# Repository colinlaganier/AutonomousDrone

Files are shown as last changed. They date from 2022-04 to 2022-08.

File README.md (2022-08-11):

# Autonomous Indoor Drone Sanitation System

## Description  

Created by Colin Laganier under the supervision of Prof. Robert Shorten as part of the MEng Final Year Project. 

Progress can be followed on the regularly update logbook for additional information about the project: [https://bit.ly/3Ni6ypL](https://bit.ly/3Ni6ypL)

## Hardware

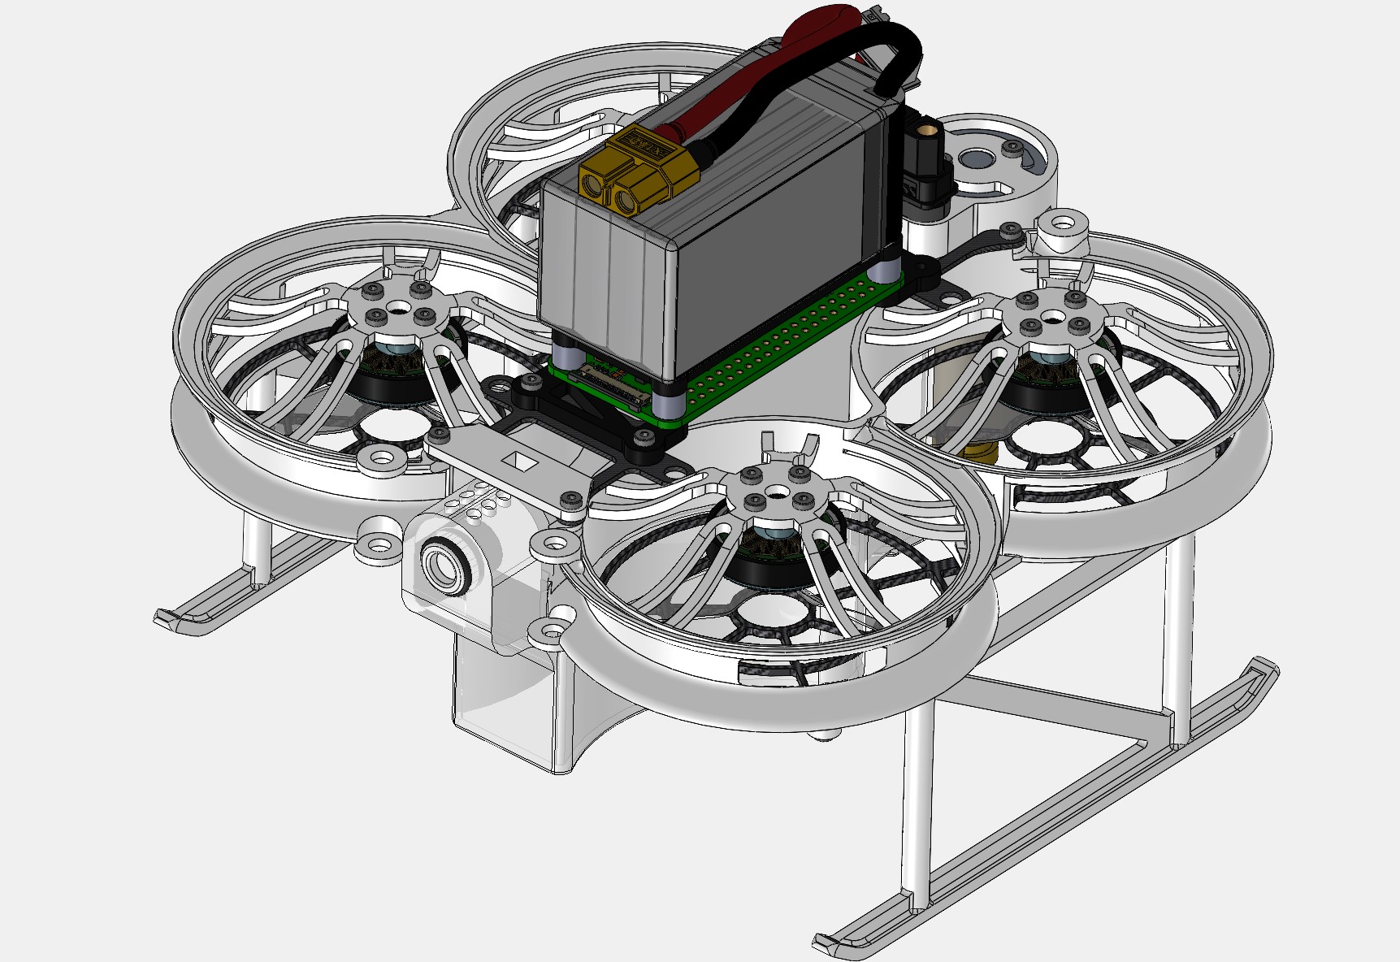
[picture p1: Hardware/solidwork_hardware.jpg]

<sub>Solidworks Hardware Assembly</sub>
<!-- &nbsp; -->
 
The drone is built upon the Diatone Taycan C25 MK2 frame, with 2004 BetaFPV brushless DC Motors and a Flywoo Goku GN745 Flight Controller ESC unit running ArduCopter 4.1.5 firmware. To fit its purpose of a sanitation drone the following pieces were designed and added:
* Transparent Nylon 100mL Water tank, fitted with a refill valve and a silicone coating to ensure watertightness.
* Waterpump and PLA support for spraying of the cleaning solution.
* Acrylic Raspberry Pi Zero support.
* PLA ski-style landing gear support legs.  

The control software is running on a Raspberry Pi Zero 2 W running Debian on each drone, connected to a central PC running Ubuntu 16.04 using a TCP/IP communication.  

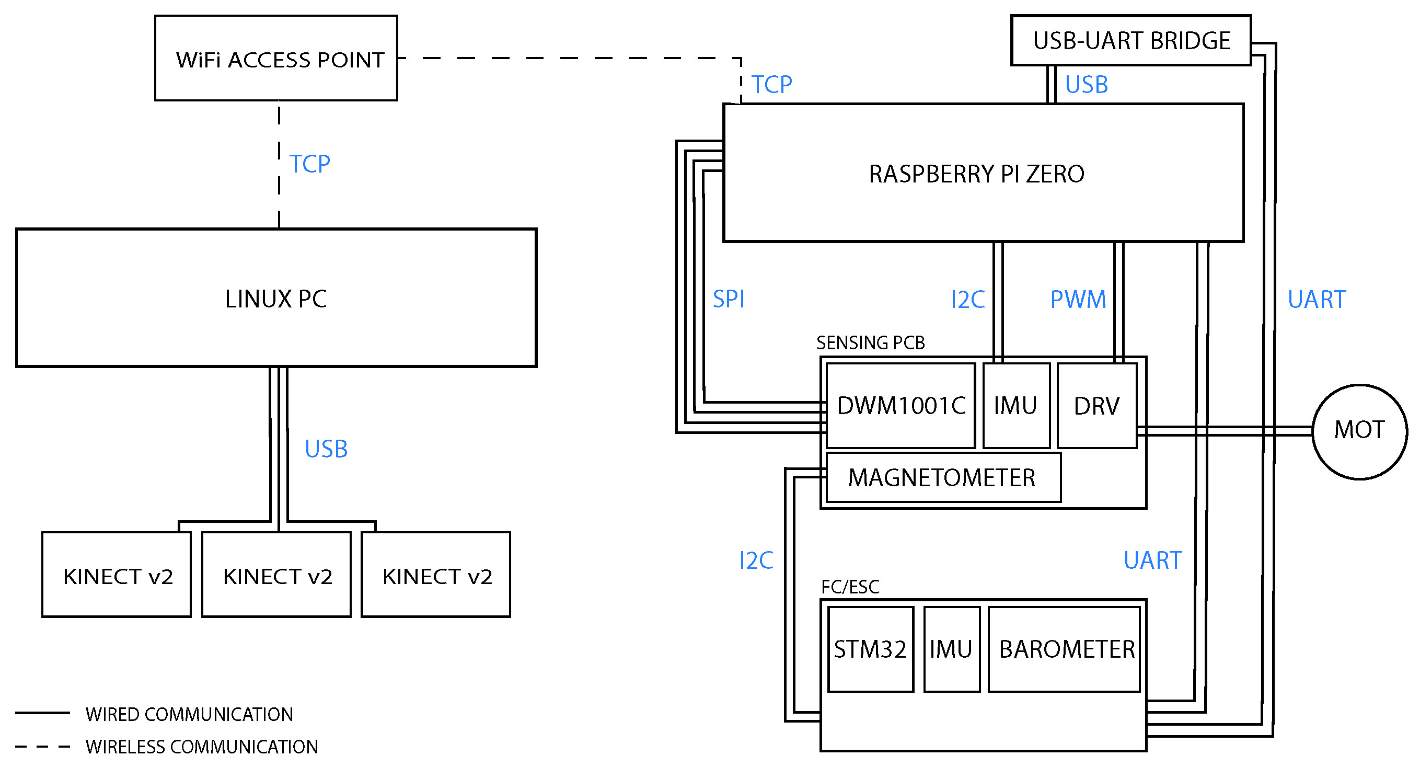
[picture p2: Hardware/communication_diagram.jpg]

<sub>Communication Architecture of Proposed Solution</sub>

## PCB


<sub>Altium Designer PCB Assembly</sub>

A custom PCB was designed to hold together the DWM1001C module from Decawave, as well as a MPU6050 IMU and a QMC5883L Compass for positioning; as well as a DRV8871 to control the spraying pump. The focus of the PCB is ensuring a small footprint to house all of the components on a small size platform. The PCB was designed with Altium Designer and manufactured and assembled by JLCPCB.

## Room Mapping

The room mapping is done using ROS running on an Linux PC using three Kinects v2 and the libfreenect2 driver with CUDA acceleration. The room mapping is done using RTAB-Map to create a 2D grid array of the furniture in the lecture hall. 

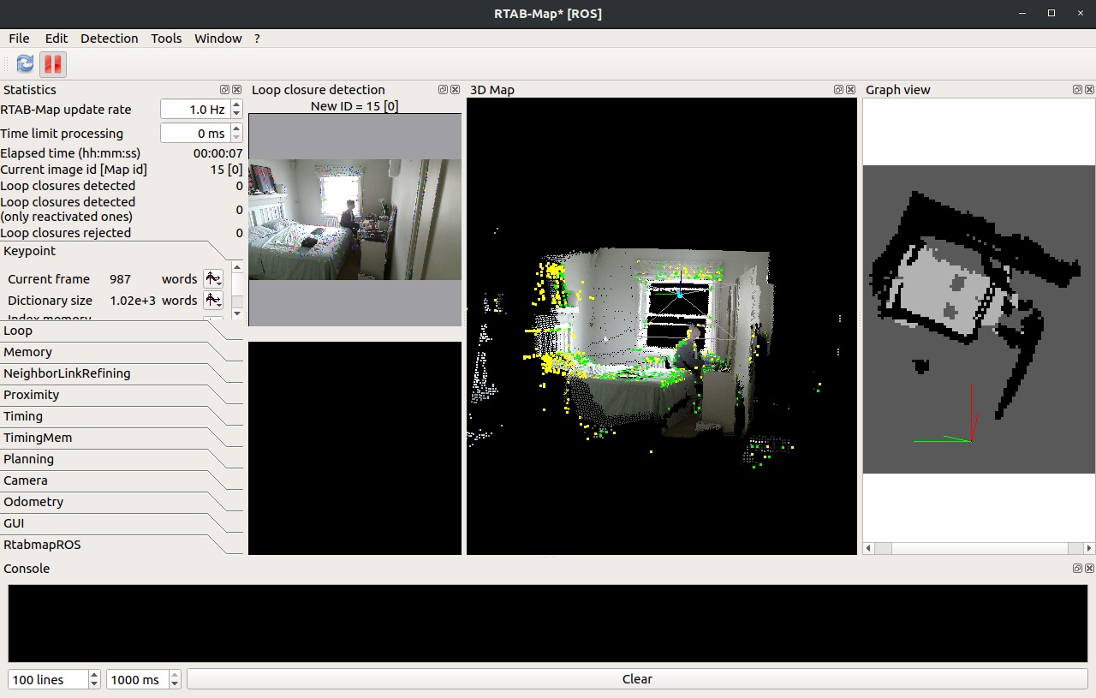
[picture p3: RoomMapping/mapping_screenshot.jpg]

<sub>Screenshot of the RTAB-Map Development GUI</sub>

## Positioning

The positioning system rely on the DWM1001C Ultra-Wideband chip by Decawave and used an asymetric two-way ranging positioning system designed by Decawave. This system provides a sub-20cm positioning error within the tested environment. The ranging data is fetched from the IC by the Raspberry Pi, reformated and fed into the Arducopter Extended Kalman Filtering positioning system where it is combined with IMU, barometer and compass data.

<p align="middle">
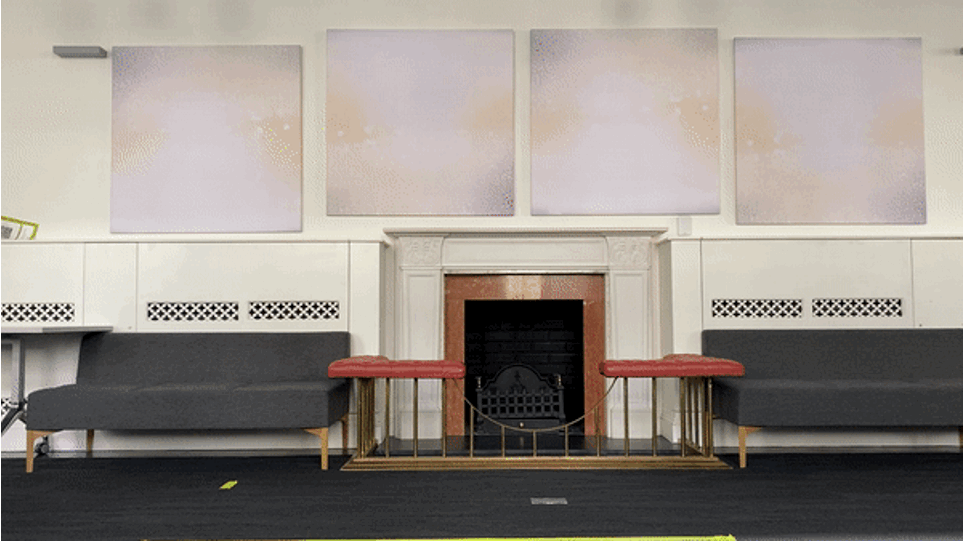
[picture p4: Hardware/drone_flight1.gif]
  
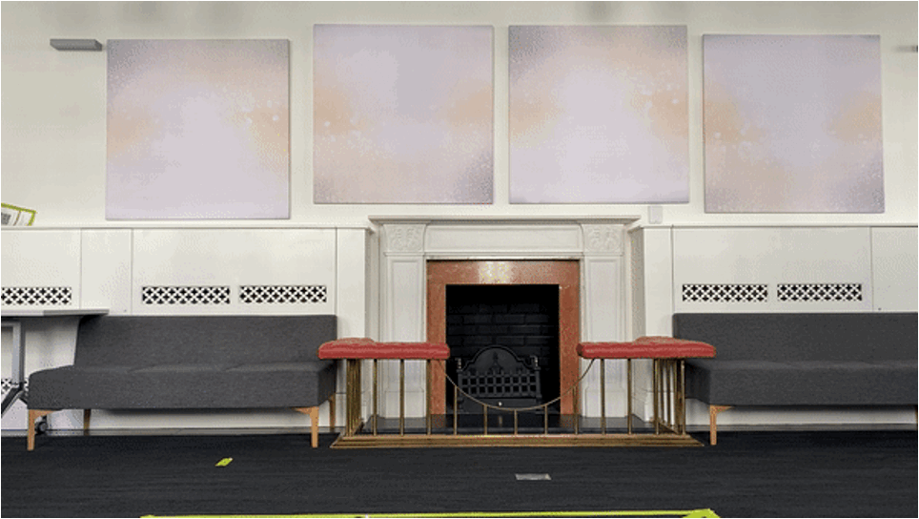
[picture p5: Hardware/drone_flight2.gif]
   
</p>

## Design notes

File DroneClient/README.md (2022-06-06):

# Drone Client

## Description 

This is the source code of the online control loop, positioning and communication. This code should be run on the drone mounted Raspberry Pi. 

To use on the Raspberry Pi, ensure the following packages are installed:
* Mavlink_v2
* WiringPi
* Pthread

To run the code, ensure the server is up and running and enter the following command in the command line from the DroneClient directory: 

```
mkdir build && cd build
cmake ../CMakeLists.txt
make 
./DroneClient
```

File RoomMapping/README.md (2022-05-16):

# Room Mapping

This directory is the ROS process to create the 2D occupancy grid from the Microsoft Kinect v2 RGBD camera using octomap.

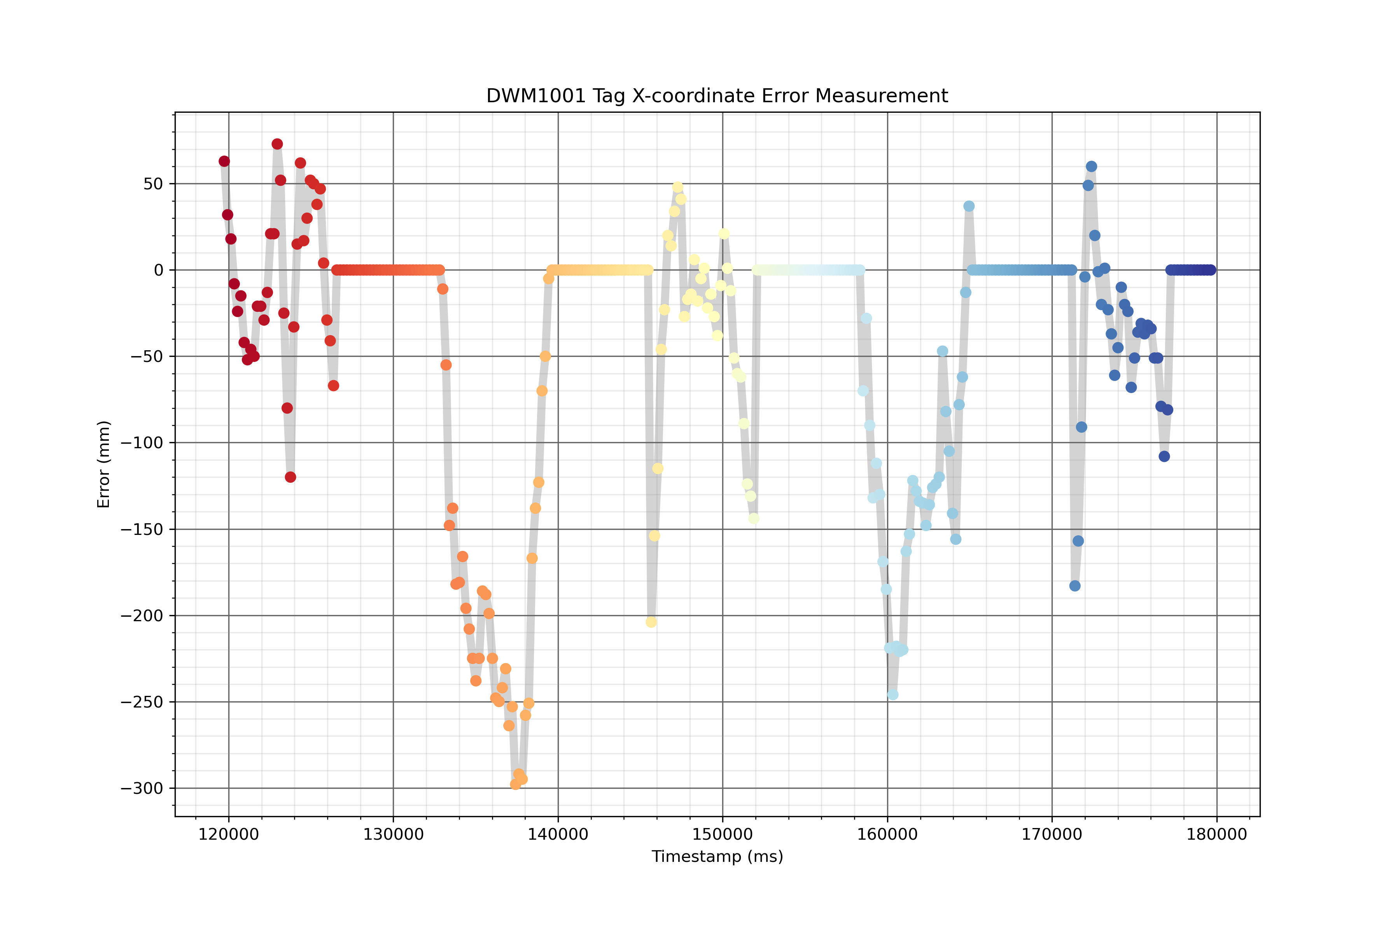
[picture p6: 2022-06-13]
Positioning/Images/error_57_x.png

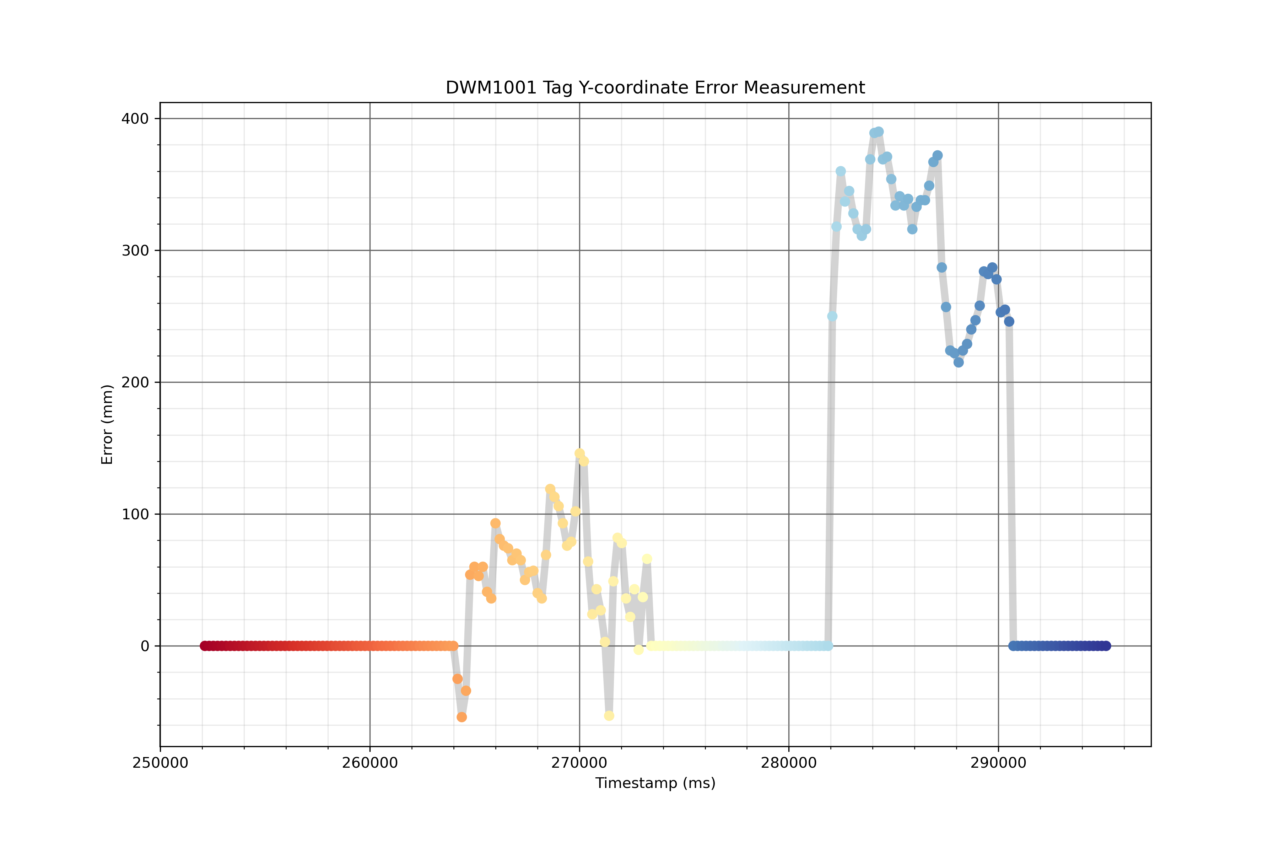
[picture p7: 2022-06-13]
Positioning/Images/error_09_y.png

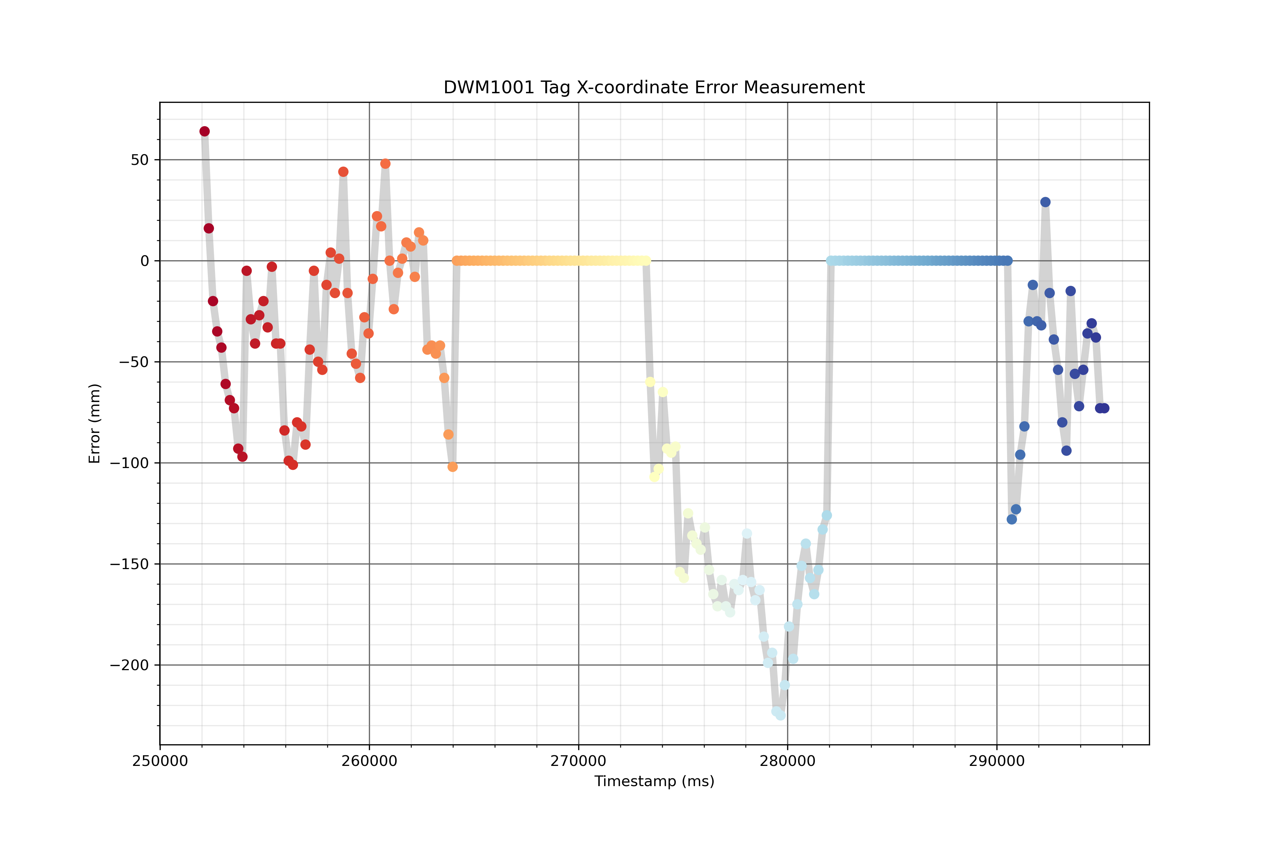
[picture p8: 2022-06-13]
Positioning/Images/error_09_x.png

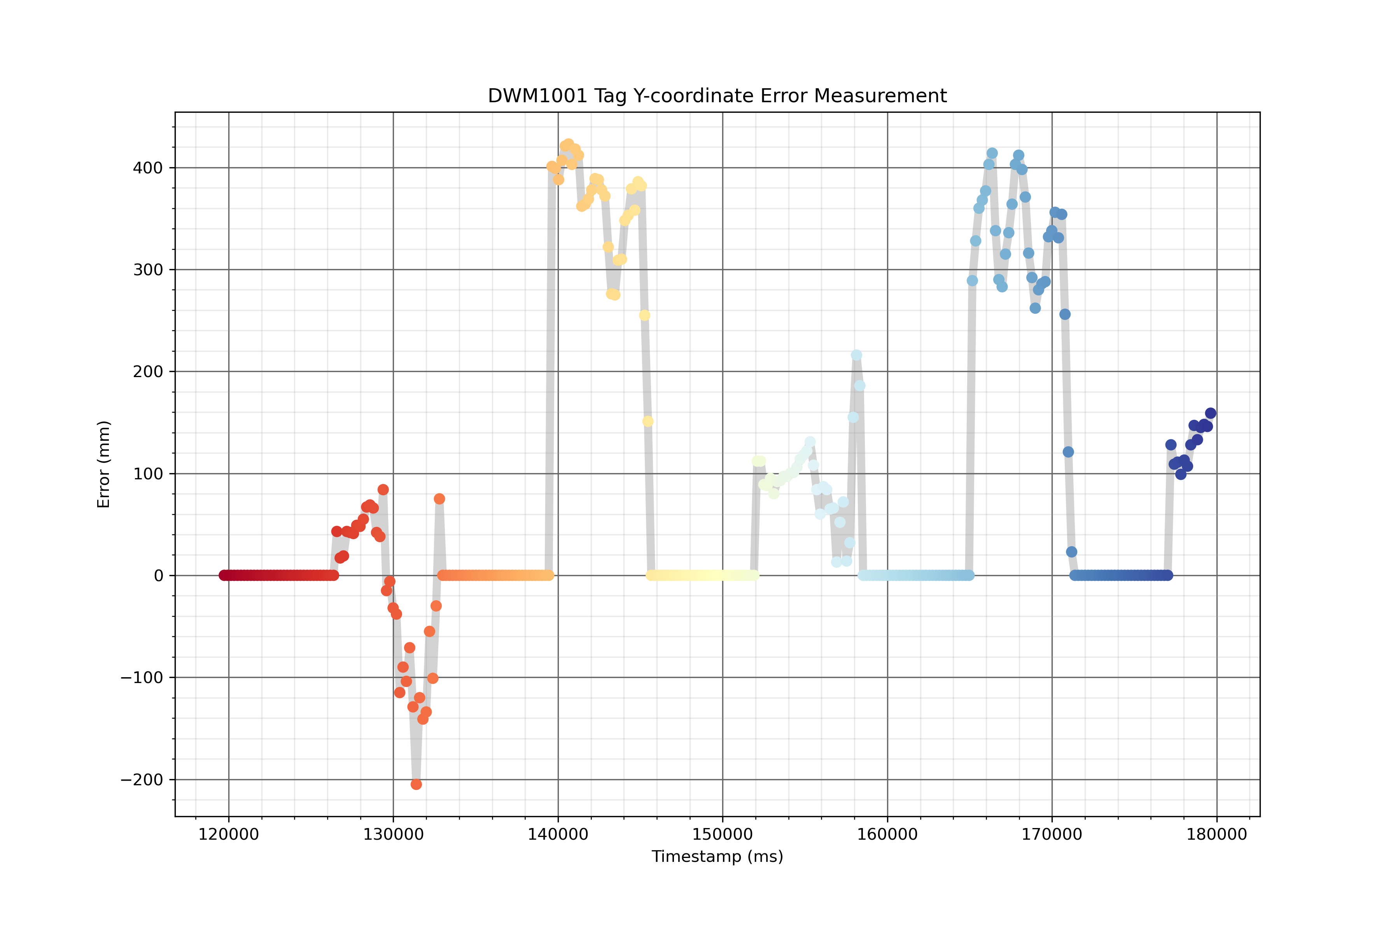
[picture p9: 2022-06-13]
Positioning/Images/error_57_y.png

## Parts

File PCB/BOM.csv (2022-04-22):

Comment | Designator | Footprint | JLCPCB Part # | Description
CL05B104KO5NNNC | C1, C3, C5, C9, C11 | 0402 | C1525 | 16V 100nF X7R ±10% 0402 Multilayer Ceramic Capacitors MLCC - SMD/SMT ROHS
CL05A106MQ5NUNC | C10 | 0402 | C15525 | 6.3V 10uF X5R ±20% 0402 Multilayer Ceramic Capacitors MLCC - SMD/SMT ROHS
EEHZA1J220XV | C2 | CAP-SMD | C454361 | 63V 22uF ±20% 8mm 80mΩ@100kHz 6.3mm 1.5A@100kHz -55℃~+105℃ 10000hrs@105℃ SMD,6.3x8mm Solid Polymer Electrolytic Capacitor ROHS
CL05B103KB5NNNC | C4 | 0402 | C15195 | 50V 10nF X7R ±10% 0402 Multilayer Ceramic Capacitors MLCC - SMD/SMT ROHS
0402B222K500NT | C6 | 0402 | C1531 | 50V 2.2nF X7R ±10% 0402 Multilayer Ceramic Capacitors MLCC - SMD/SMT ROHS
CL05B224KO5NNNC | C8, C12 | 0402 | C16772 | 16V 220nF X7R ±10% 0402 Multilayer Ceramic Capacitors MLCC - SMD/SMT ROHS
KT-0603W | D1, D2, D3 | LED_0603 | C2290 | White 0603 Light Emitting Diodes (LED) RoHS
DRV8871DDAR | IC001 | SOIC-8_3.9x4.9x1.27P | C75864 | SO-8 Motor Driver ICs ROHS
MPU-6050 | IC002 | QFN-24_EP_4.0x4.0x0.5P | C24112 | QFN-24_4x4x05P Attitude Sensors ROHS
QMC5883L | IC003 | LGA-16(3x3x0.9mm) | C976032 | LGA-16(3x3x0.9mm) Magnetic Sensors ROHS
0402WGF3002TCE | R1 | 0402 | C25776 | ±1% 1/16W Thick Film Resistors 50V ±100ppm/℃ -55℃~+155℃ 30kΩ 0402 Chip Resistor - Surface Mount ROHS
0402WGF1002TCE | R2 | 0402 | C25744 | ±1% 1/16W Thick Film Resistors 50V ±200ppm/℃ -55℃~+155℃ 30.1Ω 0402 Chip Resistor - Surface Mount ROHS
0402WGF4701TCE | R3, R4 | 0402 | C25900 | ±1% 1/16W Thick Film Resistors 50V ±100ppm/℃ -55℃~+155℃ 4.7kΩ 0402 Chip Resistor - Surface Mount ROHS
0402WGF0000TCE | R5 | 0402 | C17168 | ±1% 1/16W Thick Film Resistors 50V ±800ppm/℃ -55℃~+155℃ 0Ω 0402 Chip Resistor - Surface Mount ROHS
0402WGF2201TCE | R6, R7 | 0402 | C25879 | ±1% 1/16W Thick Film Resistors 50V ±100ppm/℃ -55℃~+155℃ 2.2kΩ 0402 Chip Resistor - Surface Mount ROHS
0402WGF301JTCE | R8, R9, R10 | 0402 | C67234 | ±1% 1/16W Thick Film Resistors 50V ±200ppm/℃ -55℃~+155℃ 30.1Ω 0402 Chip Resistor - Surface Mount ROHS
B3U-1000P | SW1, SW2 | SW-SMD-2_2.5x3.0x1.6 | C231329 | 2.5mm 1.6mm Round Button 50mA Brick nogging 3mm SPST 12V SMD,2.5x3x1.6mm Tactile Switches ROHS

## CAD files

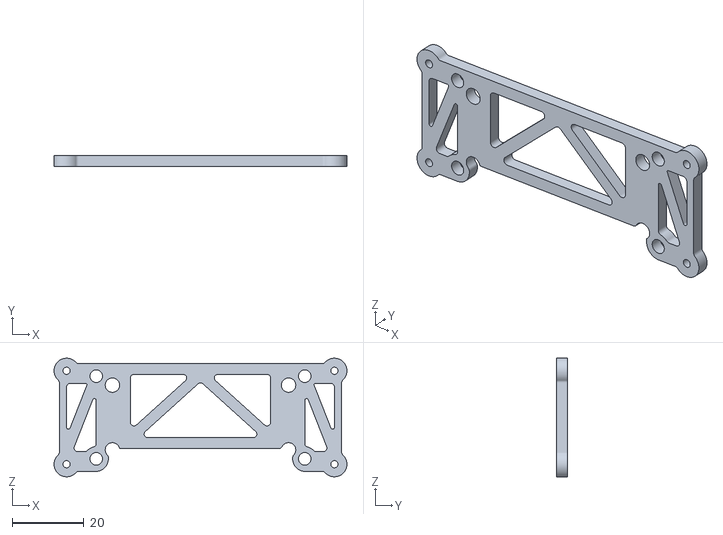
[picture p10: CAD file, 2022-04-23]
Hardware/rasPiSupport_v3.STL
81.5 x 3.00 x 33.0

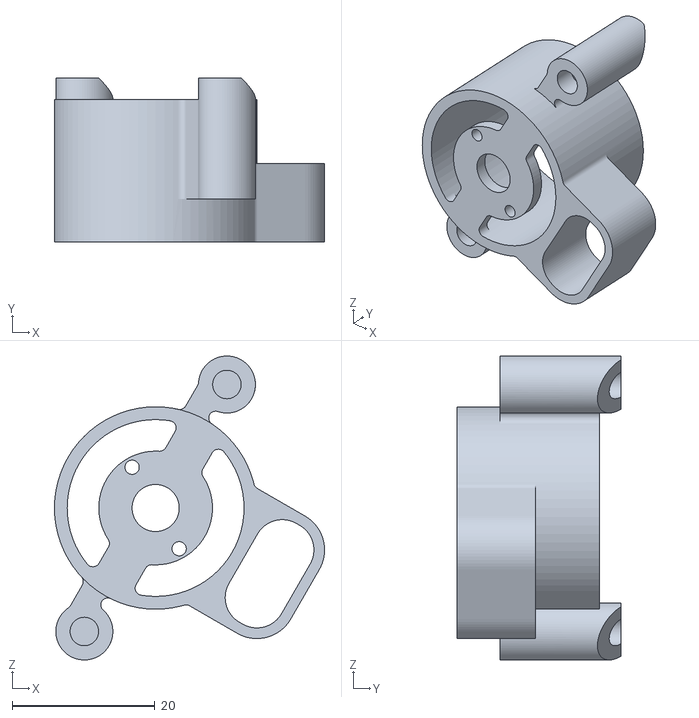
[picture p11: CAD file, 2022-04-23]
Hardware/pumpHolder_v3.STL
37.9 x 23.0 x 42.6

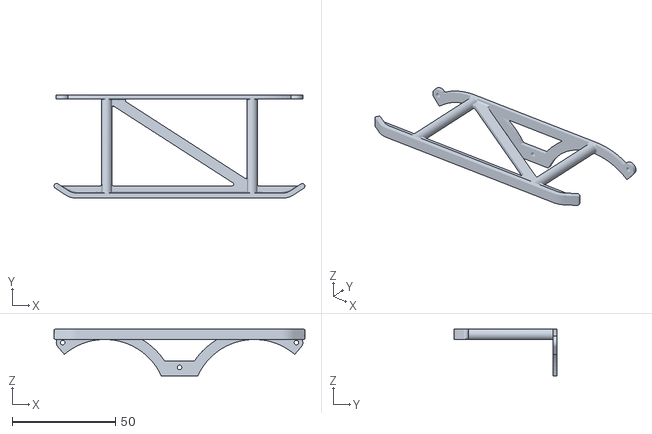
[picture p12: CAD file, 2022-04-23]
Hardware/supportRight_v2.STL
121.3 x 50.0 x 22.6

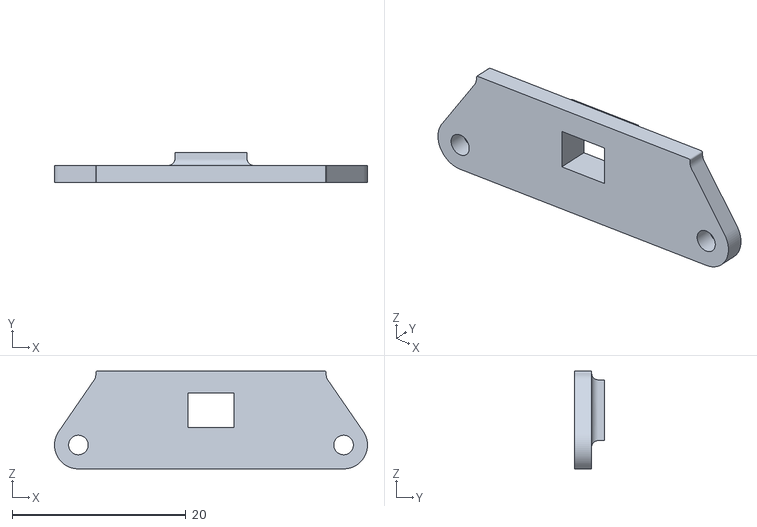
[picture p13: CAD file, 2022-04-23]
Hardware/antennaSupport_v1.STL
36.0 x 3.50 x 11.2

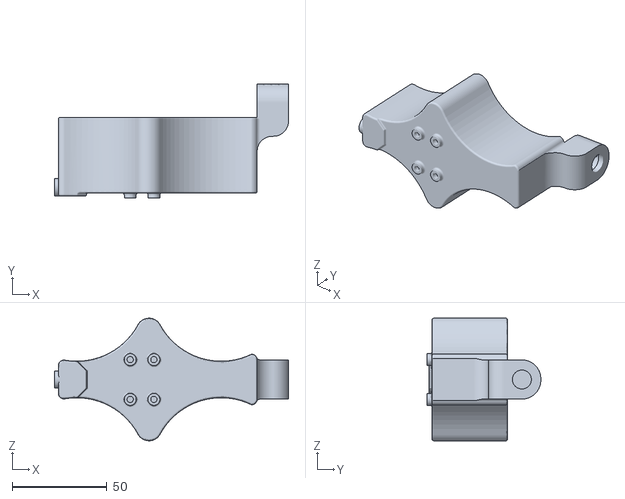
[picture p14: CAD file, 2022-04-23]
Hardware/tank_v7.STL
123.5 x 60.0 x 64.7

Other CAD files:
Hardware/supportLeft_v2.STL

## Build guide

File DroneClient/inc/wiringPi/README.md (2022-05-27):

WiringPi (Unofficial Mirror/Fork)
=================================

This is an unofficial mirror/fork of wiringPi to support ports (Python/Ruby/etc).  With the
[end of official development](http://wiringpi.com/wiringpi-deprecated/), this repository
has become a mirror of the last "official" source release, plus a fork facilitating updates
to support newer hardware (primarily for use by the ports) and fix bugs.

  * The final "official" source release can be found at the
    [`final_source_2.50`](https://github.com/WiringPi/WiringPi/tree/final_official_2.50) tag.
  * The default `master` branch contains code that has been written since that final source
    release to provide support for newer hardware.

Ports
-----

wiringPi has been wrapped for multiple languages:

* Node - https://github.com/WiringPi/WiringPi-Node
* Perl - https://github.com/WiringPi/WiringPi-Perl
* PHP - https://github.com/WiringPi/WiringPi-PHP
* Python - https://github.com/WiringPi/WiringPi-Python
* Ruby - https://github.com/WiringPi/WiringPi-Ruby

Support
-------

Please do not email Gordon if you have issues, he will not be able to help.

Pull-requests may be accepted to add or fix support for newer hardware, but new features or
other changes may not be accepted.

For support, comments, questions, etc please join the WiringPi Discord channel: https://discord.gg/SM4WUVG

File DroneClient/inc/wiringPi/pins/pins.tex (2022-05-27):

\documentclass[12pt,a4paper]{article}
\parskip 1ex
\parindent 0em
\thispagestyle{empty}
\pagestyle{plain}
\pagenumbering{arabic}
\setlength{\topmargin}{0pt}
\setlength{\headheight}{0pt}
\setlength{\headsep}{0pt}
\setlength{\topskip}{0pt}
\setlength{\textheight}{240mm}
\setlength{\footskip}{5ex}
\setlength{\oddsidemargin}{0pt}
\setlength{\evensidemargin}{0pt}
\setlength{\textwidth}{160mm}
\usepackage[dvips]{graphics,color}
\usepackage{helvet}
\renewcommand{\familydefault}{\sfdefault}
\begin{document}
\begin{sffamily}
\definecolor{rtb-black}{rgb}  {0.0, 0.0, 0.0}
\definecolor{rtb-navy}{rgb}   {0.0, 0.0, 0.5}
\definecolor{rtb-green}{rgb}  {0.0, 0.5, 0.0}
\definecolor{rtb-teal}{rgb}   {0.0, 0.5, 0.5}
\definecolor{rtb-maroon}{rgb} {0.5, 0.0, 0.0}
\definecolor{rtb-purple}{rgb} {0.5, 0.0, 0.5}
\definecolor{rtb-olive}{rgb}  {0.5, 0.5, 0.0}
\definecolor{rtb-silver}{rgb} {0.7, 0.7, 0.7}
\definecolor{rtb-grey}{rgb}   {0.5, 0.5, 0.5}
\definecolor{rtb-blue}{rgb}   {0.0, 0.0, 1.0}
\definecolor{rtb-lime}{rgb}   {0.0, 1.0, 0.0}
\definecolor{rtb-aqua}{rgb}   {0.0, 1.0, 1.0}
\definecolor{rtb-red}{rgb}    {1.0, 0.0, 0.0}
\definecolor{rtb-fuchsia}{rgb}{1.0, 0.0, 1.0}
\definecolor{rtb-yellow}{rgb} {1.0, 1.0, 0.0}
\definecolor{rtb-white}{rgb}  {1.0, 1.0, 1.0}

\begin{center}
\bfseries{WiringPi: GPIO Pin Numbering Tables}\\
\tt{https://github.com/WiringPi/WiringPi}
\end{center}

\begin{center}
\begin{tabular}{|c|c|c||p{8mm}|p{8mm}||c|c|c|c|}
\hline
\multicolumn{8}{|c|}{\bfseries{P1: The Main GPIO connector}}\\
\hline
\hline
WiringPi Pin	& BCM GPIO	& Name	& \multicolumn{2}{|c||}{Header}	& Name	& BCM GPIO	& WiringPi Pin\\
\hline
\hline
	& 			& \textcolor{rtb-red}{3.3v}	& \raggedleft{1} &  2 & \textcolor{rtb-maroon}{5v}	& 	& \\
\hline
8	& Rv1:0 - Rv2:2		& \textcolor{rtb-aqua}{SDA}	& \raggedleft{3} &  4 & \textcolor{rtb-maroon}{5v}	& 	& \\
\hline
9	& Rv1:1 - Rv2:3		& \textcolor{rtb-aqua}{SCL}	& \raggedleft{5} &  6 & \textcolor{rtb-black}{0v}	& 	& \\
\hline
7	& 4			& \textcolor{rtb-green}{GPIO7}	& \raggedleft{7} &  8 & \textcolor{rtb-yellow}{TxD}	& 14    & 15\\
\hline
	& 			& \textcolor{rtb-black}{0v}	& \raggedleft{9} & 10 & \textcolor{rtb-yellow}{RxD}	& 15	& 16\\
\hline
0	& 17			& \textcolor{rtb-green}{GPIO0}	& \raggedleft{11} & 12 & \textcolor{rtb-green}{GPIO1}	& 18	& 1\\
\hline
2	& Rv1:21 - Rv2:27	& \textcolor{rtb-green}{GPIO2}	& \raggedleft{13} & 14 & \textcolor{rtb-black}{0v}	& 	& \\
\hline
3	& 22			& \textcolor{rtb-green}{GPIO3}	& \raggedleft{15} & 16 & \textcolor{rtb-green}{GPIO4}	& 23	& 4\\
\hline
	& 			& \textcolor{rtb-red}{3.3v}	& \raggedleft{17} & 18 & \textcolor{rtb-green}{GPIO5}	& 24	& 5\\
\hline
12	& 10			& \textcolor{rtb-teal}{MOSI}	& \raggedleft{19} & 20 & \textcolor{rtb-black}{0v}	& 	& \\
\hline
13	& 9			& \textcolor{rtb-teal}{MISO}	& \raggedleft{21} & 22 & \textcolor{rtb-green}{GPIO6}	& 25	& 6\\
\hline
14	& 11			& \textcolor{rtb-teal}{SCLK}	& \raggedleft{23} & 24 & \textcolor{rtb-teal}{CE0}	& 8	& 10\\
\hline
	& 			& \textcolor{rtb-black}{0v}	& \raggedleft{25} & 26 & \textcolor{rtb-teal}{CE1}	& 7	& 11\\
\hline
\hline
WiringPi Pin	& BCM GPIO	& Name	& \multicolumn{2}{|c||}{Header}	& Name	& BCM GPIO	& WiringPi Pin\\
\hline
\end{tabular}
\end{center}

Note the differences between Revision 1 and Revision 2 Raspberry
Pi's. The Revision 2 is readily identifiable by the presence of the 2
mounting holes.

The revision 2 Raspberry Pi has an additional GPIO connector, P5, which is next to the main P1 GPIO
connector:

\begin{center}
\begin{tabular}{|c|c|c||p{8mm}|p{8mm}||c|c|c|c|}
\hline
\multicolumn{8}{|c|}{\bfseries{P5: Secondary GPIO connector (Rev. 2 Pi only)}}\\
\hline
\hline
WiringPi Pin	& BCM GPIO	& Name	& \multicolumn{2}{|c||}{Header}	& Name	& BCM GPIO	& WiringPi Pin\\
\hline
\hline
	& 		& \textcolor{rtb-maroon}{5v}	& \raggedleft{1} &  2 & \textcolor{rtb-red}{3.3v}	& 	&	\\
\hline
17	& 28		& \textcolor{rtb-green}{GPIO8}	& \raggedleft{3} &  4 & \textcolor{rtb-green}{GPIO9}	& 29	& 18	\\
\hline
19	& 30		& \textcolor{rtb-green}{GPIO10}	& \raggedleft{5} &  6 & \textcolor{rtb-green}{GPIO11}	& 31	& 20	\\
\hline
	& 		& \textcolor{rtb-black}{0v}	& \raggedleft{7} &  8 & \textcolor{rtb-black}{0v}	& 	&	\\
\hline
\hline
WiringPi Pin	& BCM GPIO	& Name	& \multicolumn{2}{|c||}{Header}	& Name	& BCM GPIO	& WiringPi Pin\\
\hline
\end{tabular}
\end{center}

\end{sffamily}
\end{document}

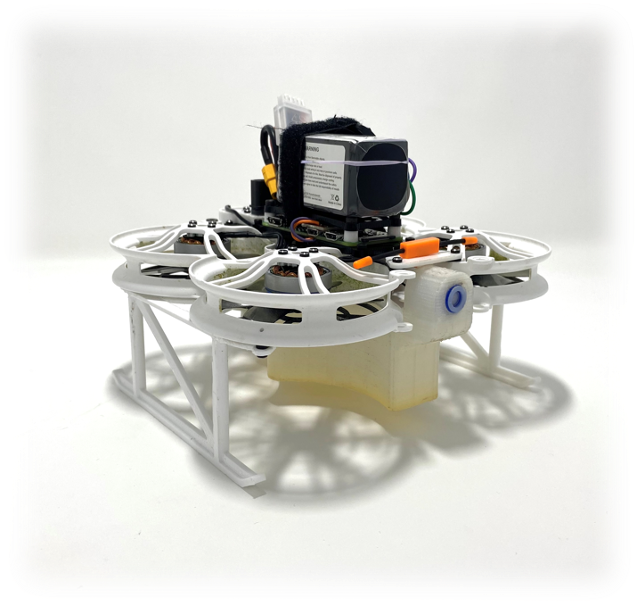
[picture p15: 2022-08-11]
Hardware/drone_assembled.png

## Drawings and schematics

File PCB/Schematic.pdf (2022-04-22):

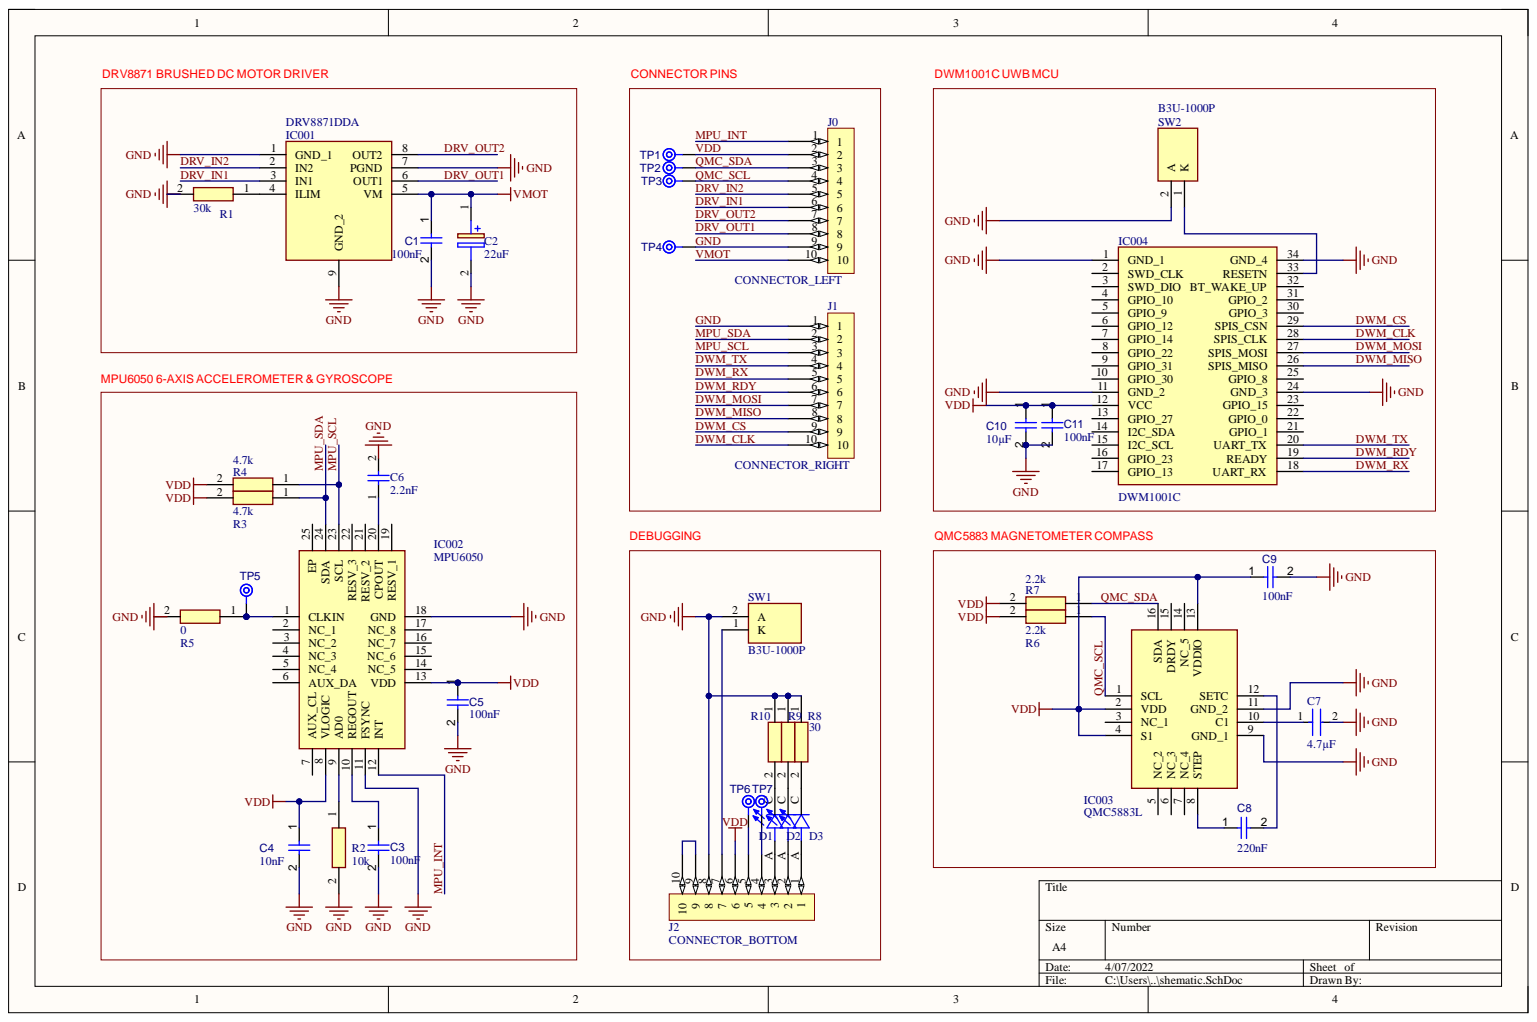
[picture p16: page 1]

1 19 CPOUT 20 RESV_2 21 RESV_3 22 SCL 23 SDA 24 EP 25

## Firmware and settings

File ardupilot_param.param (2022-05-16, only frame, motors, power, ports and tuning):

ATC_ANG_LIM_TC,1
ATC_ANG_PIT_P,18
ATC_ANG_RLL_P,18
ATC_ANG_YAW_P,10
ATC_ANGLE_BOOST,1
ATC_RAT_PIT_D,0.002
ATC_RAT_PIT_FF,0
ATC_RAT_PIT_FLTD,67
ATC_RAT_PIT_FLTE,0
ATC_RAT_PIT_FLTT,67
ATC_RAT_PIT_I,0.075
ATC_RAT_PIT_IMAX,0.5
ATC_RAT_PIT_P,0.075
ATC_RAT_PIT_SMAX,0
ATC_RAT_RLL_D,0.002
ATC_RAT_RLL_FF,0
ATC_RAT_RLL_FLTD,67
ATC_RAT_RLL_FLTE,0
ATC_RAT_RLL_FLTT,67
ATC_RAT_RLL_I,0.055
ATC_RAT_RLL_IMAX,0.5
ATC_RAT_RLL_P,0.055
ATC_RAT_RLL_SMAX,0
ATC_RAT_YAW_D,0
ATC_RAT_YAW_FF,0
ATC_RAT_YAW_FLTD,0
ATC_RAT_YAW_FLTE,2
ATC_RAT_YAW_FLTT,67
ATC_RAT_YAW_I,0.01
ATC_RAT_YAW_IMAX,0.5
ATC_RAT_YAW_P,0.1
ATC_RAT_YAW_SMAX,0
ATC_RATE_FF_ENAB,1
ATC_RATE_P_MAX,0
ATC_RATE_R_MAX,0
ATC_RATE_Y_MAX,0
BATT_AMP_OFFSET,0
BATT_AMP_PERVLT,28.5
BATT_ARM_MAH,0
BATT_ARM_VOLT,14.7
BATT_CAPACITY,3300
BATT_CRT_MAH,0
BATT_CRT_VOLT,14
BATT_CURR_PIN,12
BATT_FS_CRT_ACT,0
BATT_FS_LOW_ACT,0
BATT_FS_VOLTSRC,0
BATT_LOW_MAH,0
BATT_LOW_TIMER,10
BATT_LOW_VOLT,14.4
BATT_MONITOR,4
BATT_OPTIONS,0
BATT_SERIAL_NUM,-1
BATT_VLT_OFFSET,0
BATT_VOLT_MULT,10.9
BATT_VOLT_PIN,13
BATT2_MONITOR,0
BATT3_MONITOR,0
BATT4_MONITOR,0
BATT5_MONITOR,0
BATT6_MONITOR,0
BATT7_MONITOR,0
BATT8_MONITOR,0
BATT9_MONITOR,0
FLTMODE_CH,6
FLTMODE1,15
FLTMODE2,0
FLTMODE3,2
FLTMODE4,2
FLTMODE5,0
FLTMODE6,0
FRAME_CLASS,1
FRAME_TYPE,3
INS_GYRO_FILTER,134
INS_HNTCH_ENABLE,0
MOT_BAT_CURR_MAX,0
MOT_BAT_CURR_TC,5
MOT_BAT_IDX,0
MOT_BAT_VOLT_MAX,16.8
MOT_BAT_VOLT_MIN,13.2
MOT_BOOST_SCALE,0
MOT_HOVER_LEARN,2
MOT_PWM_MAX,2000
MOT_PWM_MIN,1000
MOT_PWM_TYPE,0
MOT_SAFE_DISARM,0
MOT_SAFE_TIME,1
MOT_SLEW_DN_TIME,0
MOT_SLEW_UP_TIME,0
MOT_SPIN_ARM,0.1
MOT_SPIN_MAX,0.95
MOT_SPIN_MIN,0.15
MOT_SPOOL_TIME,0.5
MOT_THST_EXPO,0.45
MOT_THST_HOVER,0.2
MOT_YAW_HEADROOM,200
SERIAL0_BAUD,115
SERIAL0_PROTOCOL,2
SERIAL1_BAUD,57
SERIAL1_OPTIONS,0
SERIAL1_PROTOCOL,2
SERIAL2_BAUD,57
SERIAL2_OPTIONS,0
SERIAL2_PROTOCOL,2
SERIAL3_BAUD,38
SERIAL3_OPTIONS,0
SERIAL3_PROTOCOL,23
SERIAL4_BAUD,38
SERIAL4_OPTIONS,0
SERIAL4_PROTOCOL,-1
SERIAL5_BAUD,57
SERIAL5_OPTIONS,0
SERIAL5_PROTOCOL,-1
SERIAL6_BAUD,57
SERIAL6_OPTIONS,0
SERIAL6_PROTOCOL,-1
SERIAL7_BAUD,57
SERIAL7_OPTIONS,0
SERIAL7_PROTOCOL,-1
SERVO1_FUNCTION,36
SERVO1_MAX,1900
SERVO1_MIN,1100
SERVO1_REVERSED,1
SERVO1_TRIM,1500
SERVO2_FUNCTION,33
SERVO2_MAX,1900
SERVO2_MIN,1100
SERVO2_REVERSED,1
SERVO2_TRIM,1500
SERVO3_FUNCTION,34
SERVO3_MAX,1900
SERVO3_MIN,1100
SERVO3_REVERSED,0
SERVO3_TRIM,1500
SERVO4_FUNCTION,35
SERVO4_MAX,1900
SERVO4_MIN,1100
SERVO4_REVERSED,0
SERVO4_TRIM,1500
SERVO5_FUNCTION,-1
SERVO5_MAX,1900
SERVO5_MIN,1100
SERVO5_REVERSED,0
SERVO5_TRIM,1500
SERVO6_FUNCTION,0
SERVO6_MAX,1900
SERVO6_MIN,1100
SERVO6_REVERSED,0
SERVO6_TRIM,1500
SERVO7_FUNCTION,0
SERVO7_MAX,1900
SERVO7_MIN,1100
SERVO7_REVERSED,0
SERVO7_TRIM,1500
SERVO8_FUNCTION,-1
SERVO8_MAX,1900
SERVO8_MIN,1100
SERVO8_REVERSED,0
SERVO8_TRIM,1500
SERVO9_FUNCTION,120
SERVO9_MAX,1900
SERVO9_MIN,1100
SERVO9_REVERSED,0
SERVO9_TRIM,1500

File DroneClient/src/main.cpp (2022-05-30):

/**
  **********************************************************************************
  * @file     main.cpp
  * @author   Colin Laganier
  * @version  V0.1
  * @date     2022-04-15
  * @brief   This file contains the main control script of the drone.
  **********************************************************************************
  * @attention
  */

// Include Files
#include <unistd.h>
#include <iostream>
#include <sstream>
#include <cstdlib>
#include <signal.h>
#include <chrono>
#include <unistd.h>
#include <thread>
#include <arpa/inet.h>
#include <stdio.h>
#include <string.h>
#include <sys/socket.h>
#include "atomic"

#include "DWM1001C.h"
#include "Drone.h"

#include "hal.h"
#include "dwm_api.h"

#define MESSAGE_BUFFER 128

mavlink_system_t mavlink_system = {
        1, // System ID
        1  // Component ID (MAV_COMPONENT value)
};


// Data shared between the two threads
struct Tcp_message{
    std::atomic_bool receive_flag;
    std::atomic_int send_flag;
    char send_message[MESSAGE_BUFFER];
    char receive_message[MESSAGE_BUFFER];
//    std::atomic_int send_message_len;
};

//  Function Prototypes
[[noreturn]] void control_loop(Drone *drone, Tcp_message *tcp_message, DWM1001C *dwm);
//[[noreturn]] void control_loop(Drone *drone, Tcp_message *tcp_message);
[[noreturn]] void tcp_handler(int socket, char buffer[], Tcp_message *message);
void identify_message(Drone *drone, char message[], int message_head, char *message_response);
void send_tcp_message(Tcp_message *tcp_message, char *message);
void tcp_set_message(Tcp_message *message_object, char *new_message, bool send_or_receive);

//Tcp_message::Tcp_message(send_bool, receive_bool, send_char, send_int) {

//}

int main(){
    setvbuf(stdout, NULL, _IONBF, 0);
    std::cout << "Drone Startup\n";
    Drone drone;
    DWM1001C dwm;

    ///////////////////////////////////////////////////////////////////////////////////////////////////////////////////
    // TCP Socket communication parameters
    int server_socket = 0;
    struct sockaddr_in server_address;
//    char* handshake_message;
    char buffer[MESSAGE_BUFFER];

    // Initialising variables
    Tcp_message tcp_message;
    tcp_message.send_flag = -1;
    tcp_message.receive_flag = false;
//    tcp_message.send_message_len = MESSAGE_BUFFER;
    char tcp_init_message[] = " ";
    tcp_set_message(&tcp_message, tcp_init_message, true);
    tcp_set_message(&tcp_message, tcp_init_message, false);

    if ((server_socket = socket(AF_INET, SOCK_STREAM, 0)) < 0) {
        std::cout << "\n Socket creation error \n";
        return -1;
    }

    server_address.sin_family = AF_INET;
    server_address.sin_port = htons((uint16_t)drone.drone_port);

    // Convert IPv4 and IPv6 addresses from text to binary
    if (inet_pton(AF_INET, drone.server_ip.c_str(), &server_address.sin_addr)<= 0) {
        std::cout << "\nInvalid address/ Address not supported \n";
        return -1;
    }

    if (connect(server_socket, (struct sockaddr*)&server_address,sizeof(server_address)) < 0) {
        std::cout << "\nConnection Failed \n";
        return -1;
    }
    else
        drone.toggle_sensor_tcp();

    // Verifies connection confirmation from server
    read(server_socket, buffer, MESSAGE_BUFFER);
    std::cout << "Connection confirmation:" << buffer << "\n";

    ///////////////////////////////////////////////////////////////////////////////////////////////////////////////////
    // Initializing UART communication

//    if (drone.setup_serial() > 0) {
//        std::cout << "Error initialising UART \n";
//        return -1;
//    }

    ///////////////////////////////////////////////////////////////////////////////////////////////////////////////////

    dwm.dwm_setup();
    if (dwm.dwm_setup_serial() == 1){
        std::cout << "UWB Serial setup error\n";
        return -1;
    }
    if (dwm.dwm_verify_config()) {
        std::cout << "UWB Setup Complete";
        drone.toggle_sensor_uwb();
    }

    ///////////////////////////////////////////////////////////////////////////////////////////////////////////////////

    if (drone.drone_ready())
    {
        printf("Drone ready\n");
        // Create separate threads to receive base station commands while running
//        std::thread network_thread(tcp_handler, server_socket, buffer, &tcp_message);
        std::thread control_thread(control_loop, &drone, &tcp_message, &dwm);
//        std::thread control_thread(control_loop, &drone, &tcp_message);

//        network_thread.join();
        control_thread.join();
    }
    return 0;
}

[[noreturn]] void tcp_handler(int socket, char buffer[], Tcp_message *message){
    std::cout << "TCP Communication thread started\n";

    int index = 0;


    while(index < 3)
    {
        index++;
        if (message->send_flag){
            send(socket, message->send_message, MESSAGE_BUFFER, 0);
            message->send_flag = false;
        }
        else
//        val_read =
        read(socket, buffer, 1024);
        std::cout << "Read message:" << buffer << "\n";
        message->receive_flag = true;
        tcp_set_message(message, buffer, false);
   }
}

void send_tcp_message(Tcp_message *tcp_message, char *message){
    tcp_set_message(tcp_message, message, true);
}

FLIGHT_MODE identify_mode(char *mode_request){
    const char *mode_guided = "Guided";
    const char *mode_stabilize = "Stabilize";
    const char *mode_althold = "AltitudeHold";
    const char *mode_loiter = "Loiter";
    const char *mode_poshold = "PositionHold";
    const char *mode_rtl = "RTL";
    const char *mode_auto = "Auto";

    if (mode_request == mode_guided)
        return GUIDED_NOGPS;
    else if (mode_request == mode_stabilize)
        return STABILIZE;
    else if (mode_request == mode_althold)
        return ALT_HOLD;
    else if (mode_request == mode_loiter)
        return LOITER;
    else if (mode_request == mode_poshold)
        return POS_HOLD;
    else if (mode_request == mode_rtl)
        return RTL;
    else if (mode_request == mode_auto)
        return AUTO;
    return STABILIZE;
}


void identify_message(Drone *drone, char message[], int message_head, char *message_response){
    // Message format int:char[] -> ex: "1:Stabilize\0"
    char* message_tail;
    if (message[1] == ':'){
        message_tail = message + 2;
        std::cout << message_tail << '\n';
    }
    switch (message_head) {
        case -1: {
            std::cout << "idle mode";
            break;
        }
        case 0: {
            // Setup Mode
            if (drone->mavlink_positioning_status())
                drone->toggle_sensor_uwb();

            std::cout << "Check setup";
            break;
        }
        case 1: {
            // Set flight mode
            FLIGHT_MODE new_mode = identify_mode(message_tail);
            drone->mavlink_set_flight_mode(new_mode);
            while((drone->get_mode() != new_mode)){
                drone->mavlink_receive_data();
                drone->mavlink_set_flight_mode(new_mode);
            }
            std::cout << "Flight mode set to: " << message_tail << ", mode: " << new_mode << '\n';
            sleep(0.5);
            break;
        }
        case 2: {
            // Guided coordinates
            break;
        }
        case 3:{
            drone->mavlink_arm();
            drone->state = ARMED_STATE;
            strcpy(message_response, "Drone Armed");
            // Arm Motors
//            if (drone->drone_sensor.uwb){
//                if (drone->flight_mode == STABILIZE || drone->flight_mode == AUTO) {
//                    drone->mavlink_arm();
//                    drone->state = ARMED_STATE;
//                    message_response = "Drone armed";
//                }
//                else {
//                    message_response = "Flight mode not set to stabilize";
//                }
//            }
//            message_response = "Positioning not ready";
            break;
        }
        case 4:{
            if (drone->state == ARMED_STATE && drone->flight_mode == AUTO){
//                drone->mavlink_takeoff();
                std::cout << "Takeoff\n";
//                drone->state = STATIONARY;
            }

            // Take off
            break;
        }
        case 5: {
            // Stabilize
            drone->mavlink_disarm();
            drone->state = DISARMED;
            strcpy(message_response, "Drone Disarmed");

            break;
        }
        case 6: {
            // Guided mode
            break;
        }
	case 7: {
            // Return home
            break;
        }
        case 8: {
            // Land
            break;
        }
         default:
            break;

    }
}

void tcp_set_message(Tcp_message *message_object, char *new_message, bool send_or_receive){
    char *destination;
    destination = (send_or_receive) ? message_object->send_message :  message_object->receive_message;
    strncpy(destination, new_message, MESSAGE_BUFFER);
    *(destination+ MESSAGE_BUFFER) = 0;
//    message_object->send_message_len = strlen(new_message);
    std::cout << strlen(new_message) << '\n';
}

[[noreturn]] void control_loop(Drone *drone, Tcp_message *tcp_message, DWM1001C *dwm){
    char message_response[256];
    static uint32_t loop_start = 0;
    static uint8_t stage = 0;   // 0 = initialisation, 1 = normal flight
    static uint16_t beacon_sent_count = 0;
    static uint32_t beacon_sent_time = 0;
    uint8_t counter = 0;

    while (true) {
        // Send heartbeat at a ~1Hz frequency
//        unsigned long mavlink_current_heartbeat = millis();
//        if (mavlink_current_heartbeat - drone->mavlink_previous_heartbeat >= drone->mavlink_interval_heartbeat) {
//            drone->mavlink_previous_heartbeat = mavlink_current_heartbeat;
//            drone->mavlink_heartbeat();
//            drone->number_hbs++;

            // Periodic FC data request
//            if (drone->number_hbs >= drone->setup_hbs){
//                std::cout << "Requesting Data \n";
//                drone->mavlink_request_data();
//                drone->number_hbs = 0;
//            }
//        }

        // Fetch uwb positioning
//        unsigned long uwb_current_sensing = millis();
////        std::cout << uwb_current_sensing << '\n';
//        if ((uwb_current_sensing - dwm->uwb_last_sensing ) > dwm->wait_period){
////            std::cout << "UWB measurement \n";
//            dwm->uwb_last_sensing = uwb_current_sensing;
//            std::cout << "Number of anchors: " << (int)dwm->loc.anchors.dist.cnt << '\n';
//
//            if(dwm_loc_get(&(dwm->loc)) == RV_OK)
//            {
//                HAL_Print("\t[%d,%d,%d,%u]\n", dwm->loc.p_pos->x, dwm->loc.p_pos->y, dwm->loc.p_pos->z,
//                          dwm->loc.p_pos->qf);
//
//                for (int i = 0; i < dwm->loc.anchors.dist.cnt; ++i)
//                {
//                    HAL_Print("\t%u)", i);
//                    HAL_Print("0x%llx", dwm->loc.anchors.dist.addr[i]);
//                    if (i < dwm->loc.anchors.an_pos.cnt)
//                    {
//                        HAL_Print("[%d,%d,%d,%u]", dwm->loc.anchors.an_pos.pos[i].x,
//                                  dwm->loc.anchors.an_pos.pos[i].y,
//                                  dwm->loc.anchors.an_pos.pos[i].z,
//                                  dwm->loc.anchors.an_pos.pos[i].qf);
//                    }
//                    HAL_Print("=%u,%u\n", dwm->loc.anchors.dist.dist[i], dwm->loc.anchors.dist.qf[i]);
//
//                }
//            }
//        }
        // advance to normal flight stage after 1min
        if (stage == 0) {
            uint32_t time_diff =  (millis() - loop_start);
            if (time_diff > 60000) {
                stage = 1;
                std::cout << "Stage1\n";
            }
        }

        // slow down counter
        counter++;
        if (counter >= 20) {
            counter = 0;
        }
        if (stage == 0 || counter == 0) {
            dwm->dwm_send_beacon_config();
            dwm->dwm_get_position();
            if (beacon_sent_count > 0 && beacon_sent_time != 0) {
                uint32_t time_diff = millis() - beacon_sent_time;
                float hz = (float)beacon_sent_count / (time_diff / 1000.0f);
                std::cout << "Beacon hz:" << hz << '\n';
            }
            beacon_sent_count = 0;
            beacon_sent_time = millis();
        }

        // send beacon distances
        dwm->dwm_get_ranges();
        beacon_sent_count++;


        // Check if TCP command received from Ground Station
//        if (tcp_message->receive_flag){
////            std::cout << "Received message\n";
//            int message_head = (int)tcp_message->receive_message[0];
//            if (message_head != drone->get_state()){
//                identify_message(drone, tcp_message->receive_message, message_head, message_response);
//                tcp_set_message(tcp_message, message_response, true);
//            }
//        }

//        if (drone->state == TAKEOFF)
//            std::cout <<

        //  Receiving MAVLINK data
//        drone->mavlink_receive_data();

        // Toggle spray if over a table
//        if (drone->spray_state != drone->identify_table())
//            drone->toggle_pump();

    }
}

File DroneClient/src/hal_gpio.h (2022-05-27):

/*! ------------------------------------------------------------------------------------------------------------------
 * @file    hal_gpio.h
 * @brief   utility to operate GPIOs
 *          this lib is Raspberry-Pi dependent
 *
 * @attention
 *
 * Copyright 2017 (c) Decawave Ltd, Dublin, Ireland.
 *
 * All rights reserved.
 *
 */
#ifndef _HAL_GPIO_H_
#define _HAL_GPIO_H_

#ifdef __cplusplus
extern "C" {
#endif

#include <wiringPi.h>

#define HAL_GPIO_INT_EDGE_FALLING   INT_EDGE_FALLING
#define HAL_GPIO_INT_EDGE_RISING    INT_EDGE_RISING
#define HAL_GPIO_INT_EDGE_BOTH      INT_EDGE_BOTH   
#define HAL_GPIO_INT_EDGE_SETUP     INT_EDGE_SETUP

#define HAL_GPIO_DRDY  3

/** 
 * @brief initializes the GPIO utilities
 *
 * @param none
 *
 * @return Error code
 */
int HAL_GPIO_Init(void);

/** 
 * @brief setup pin interrupt callback function on certain condition
 *
 * @param [in] pin: GPIO pin number of the Raspberry Pi external connector.
 * @param [in] edge_type: GPIO edge type to trigger interrupt
 * @param [in] cb: callback function pointer to be called when interrupt on the pin happens. 
 *
 * @return Error code
 */
int HAL_GPIO_SetupCb(int pin, int edge_type, void (*cb)(void));

/** 
 * @brief Reads the GPIO pin
 *
 * @param [in] pin: GPIO pin to be read.
 *
 * @return GPIO value
 */
int HAL_GPIO_PinRead(int pin);

#ifdef __cplusplus
}
#endif

#endif //_HAL_GPIO_H_

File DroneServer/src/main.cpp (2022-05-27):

#include <cstdio>
#include <cstring>   //strlen
#include <cstdlib>
#include <cerrno>
#include <unistd.h>   //close
#include <arpa/inet.h>    //close
#include <sys/types.h>
#include <sys/socket.h>
#include <netinet/in.h>
#include <ctime>

#define TRUE   1
#define FALSE  0
#define PORT 8888

int main(int argc , char *argv[]) {
    int opt = TRUE;
    int master_socket, addrlen, new_socket, client_socket[30], max_clients = 3, activity, i, valread, sd;
    int max_sd;
    struct sockaddr_in address;

    char buffer[1025];  //data buffer of 1K

    //set of socket descriptors
    fd_set readfds;

    //a message
    char *message = "ECHO Daemon v1.0 \r\n";

    //initialise all client_socket[] to 0 so not checked
    for (i = 0; i < max_clients; i++) {
        client_socket[i] = 0;
    }

    //create a master socket
    if ((master_socket = socket(AF_INET, SOCK_STREAM, 0)) == 0) {
        perror("socket failed");
        exit(EXIT_FAILURE);
    }

    //set master socket to allow multiple connections
    if (setsockopt(master_socket, SOL_SOCKET, SO_REUSEADDR, (char *) &opt, sizeof(opt)) < 0) {
        perror("setsockopt");
        exit(EXIT_FAILURE);
    }

    //type of socket created
    address.sin_family = AF_INET;
    address.sin_addr.s_addr = INADDR_ANY;
    address.sin_port = htons(PORT);

    //bind the socket to localhost port 8888
    if (bind(master_socket, (struct sockaddr *) &address, sizeof(address)) < 0) {
        perror("bind failed");
        exit(EXIT_FAILURE);
    }
    printf("Listener on port %d \n", PORT);

    //try to specify maximum of 3 pending connections for the master socket
    if (listen(master_socket, 3) < 0) {
        perror("listen");
        exit(EXIT_FAILURE);
    }

    //accept the incoming connection
    addrlen = sizeof(address);
    puts("Waiting for connections ...");

    while (TRUE) {
        //clear the socket set
        FD_ZERO(&readfds);

        //add master socket to set
        FD_SET(master_socket, &readfds);
        max_sd = master_socket;

        //add child sockets to set
        for (i = 0; i < max_clients; i++) {
            //socket descriptor
            sd = client_socket[i];

            //if valid socket descriptor then add to read list
            if (sd > 0)
                FD_SET(sd, &readfds);

            //highest file descriptor number, need it for the select function
            if (sd > max_sd)
                max_sd = sd;
        }

        //wait for an activity on one of the sockets , timeout is NULL ,
        //so wait indefinitely
        activity = select(max_sd + 1, &readfds, nullptr, nullptr, nullptr);

        if ((activity < 0) && (errno != EINTR)) {
            printf("select error");
        }

        //If something happened on the master socket ,
        //then it's an incoming connection
        if (FD_ISSET(master_socket, &readfds)) {
            if ((new_socket = accept(master_socket,
                                     (struct sockaddr *) &address, (socklen_t *) &addrlen)) < 0) {
                perror("accept");
                exit(EXIT_FAILURE);
            }

            //inform user of socket number - used in send and receive commands
            printf("New connection , socket fd is %d , ip is : %s , port : %d\n", new_socket,
                   inet_ntoa(address.sin_addr), ntohs(address.sin_port));

            //send new connection greeting message
            if (send(new_socket, message, strlen(message), 0) != strlen(message)) {
                perror("send");
            }

            puts("Welcome message sent successfully");

            //add new socket to array of sockets
            for (i = 0; i < max_clients; i++) {
                //if position is empty
                if (client_socket[i] == 0) {
                    client_socket[i] = new_socket;
                    printf("Adding to list of sockets as %d\n", i);

                    break;
                }
            }
        }

        //else it's some IO operation on some other socket
        for (i = 0; i < max_clients; i++) {
            sd = client_socket[i];

            if (FD_ISSET(sd, &readfds)) {
                //Check if it was for closing , and also read the
                //incoming message
                if ((valread = read(sd, buffer, 1024)) == 0) {
                    //Somebody disconnected , get his details and print
                    getpeername(sd, (struct sockaddr *) &address, (socklen_t *) &addrlen);
                    printf("Host disconnected , ip %s , port %d \n",
                           inet_ntoa(address.sin_addr), ntohs(address.sin_port));

                    //Close the socket and mark as 0 in list for reuse
                    close(sd);
                    client_socket[i] = 0;
                }

                    //Echo back the message that came in
                else {
                    //set the string terminating NULL byte on the end
                    //of the data read
                    buffer[valread] = '\0';
                    printf("Received message\n");
                    printf(buffer);
//                    send(sd , buffer , strlen(buffer) , 0 );
                }
            }
        }
    }
}

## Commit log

2022-04-19 initial TCP/IP socket
2022-04-22 Added PCB Gerber files
    [BOM.xlsx, P&P.csv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]
2022-04-22 Added PCB schematic and render
    [BOM.csv, BOM.xlsx, P&P.csv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]
2022-04-23 Restructured directory
    [PCB_v5.GBL, PCB_v5.GBO, PCB_v5.GBS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]
2022-04-23 Added STL files
    [RasPiSupport_v1.STL, antennaSupport_v1.STL, pumpHolder_v3.STL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]
2022-04-23 added more hardware files
    [RasPiSupport_v1.STL, rasPiSupport_v3.STL, supportLeft_v2.STL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]
2022-05-04 added socket and start of code
2022-05-08 Base Drone class and TCP client socket
2022-05-11 Threading tested and functionning
2022-05-13 Added ardupilot parameter file
    [ardupilot_param.param]
2022-05-23 Integrated MAVLINK and DWM1001 with bugs
    [DWM1001C.cpp, DWM1001C.h, dwm1001_tlv.h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]
2022-06-06 Added sensor testing
2022-06-07 Added positioning data & visualisation
    [2022-06-06-14-18-57.csv, 2022-06-06-14-21-09.csv, 2022-06-06-14-22-28.csv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]
2022-06-13 Added positioning data analysis
    [2022-06-06-14-18-57.csv, 2022-06-06-14-21-09.csv, 2022-06-06-14-21-09_analysis.xlsx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]
